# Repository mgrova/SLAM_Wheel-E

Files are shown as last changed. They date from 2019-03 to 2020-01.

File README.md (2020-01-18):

# SLAM_Wheel-E
Este es un proyecto en el cual se busca realizar una comparativa de diferentes técnicas de SLAM empleando un robot movil diferencial tipo Rover.

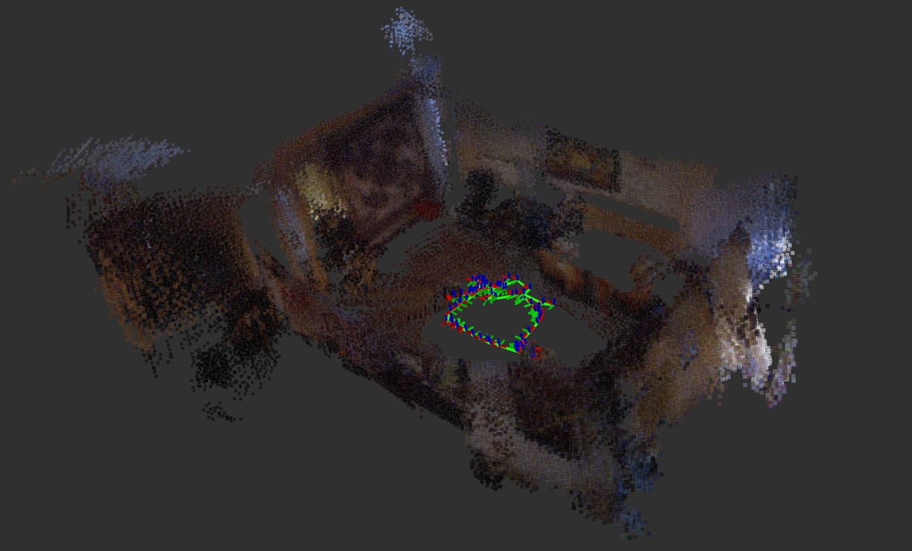
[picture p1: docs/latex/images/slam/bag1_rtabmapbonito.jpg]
RTABmap


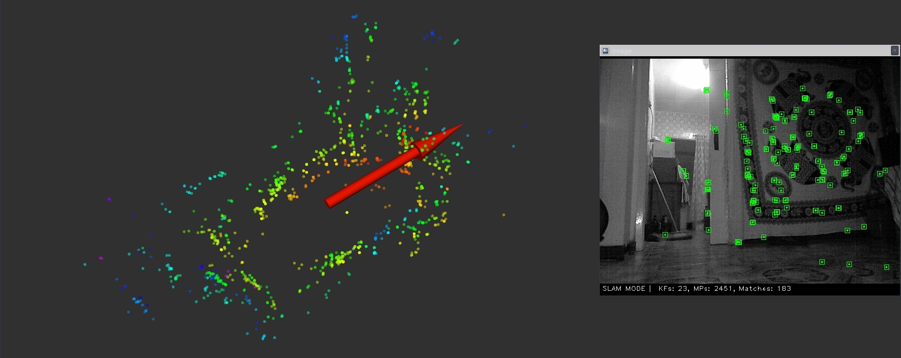
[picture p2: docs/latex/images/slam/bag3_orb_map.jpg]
ORB


# Wheel-E 
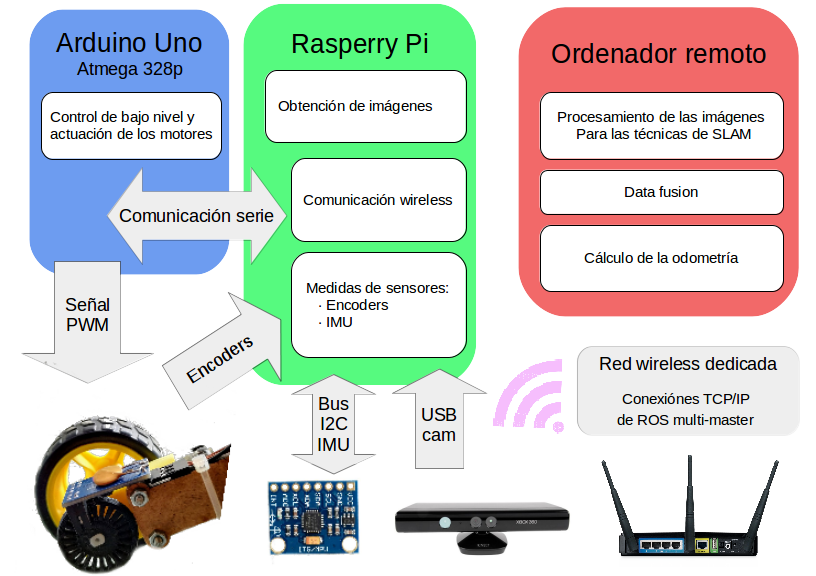
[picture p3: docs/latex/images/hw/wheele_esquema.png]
wheele_esquema


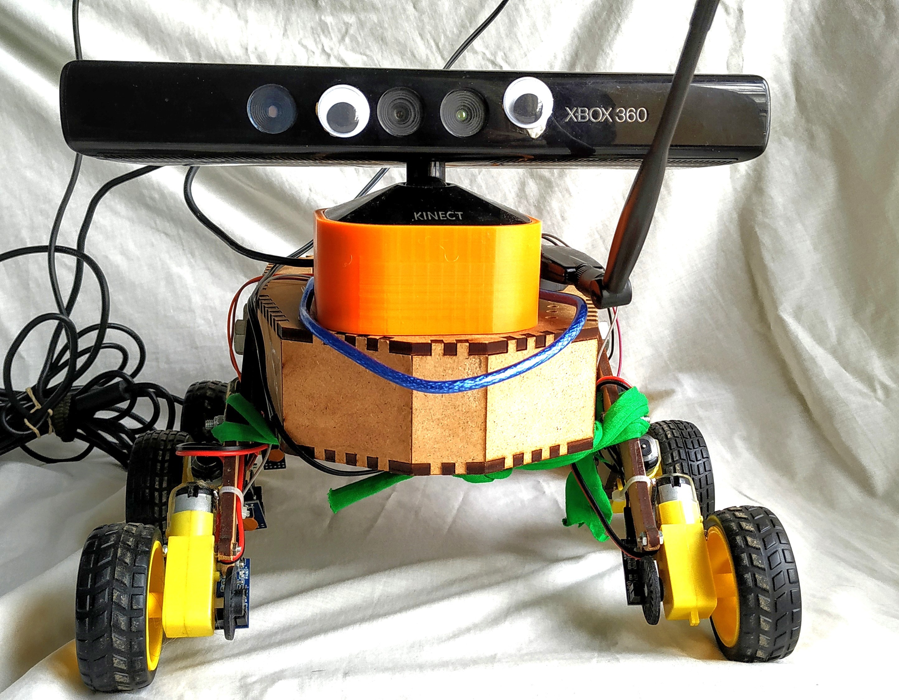
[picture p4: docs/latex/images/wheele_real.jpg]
wheele


Un análisis en detalle de todo el proyecto, así como de sus resultados se encuentra (en español) [aquí](doc.md). Los recursos bibliográficos disponibles se pueden consultar en [docs/](SLAM_Wheel-E/docs/). 

# DEPENDENCIAS
## Uso de lod gpio de la RPi
Se hace uso de la libreria pigpio:(http://abyz.me.uk/rpi/pigpio/download.html)

```
wget abyz.me.uk/rpi/pigpio/pigpio.tar
tar xf pigpio.tar
cd PIGPIO
make
sudo make install
```

## Comunicación Serial RPi-Arduino
Se hará uso de la librería de Python:

https://github.com/harmsm/PyCmdMessenger

Destacar que se emplará python2.7 y no python3.

## Comunicación multimaster(https://wiki.ros.org/multimaster_fkie)
Para comunicar la RPi y el PC, es necesario tener instalado el siguiente paquete:

```
sudo apt install ros-kinetic-multimaster-fkie
sudo apt install ros-kinetic-multimaster-launch
```

## Drivers Kinect v1 (RGB-D Camera)
Se emplearán tanto los driver necesarios para leer la IMU de la cámara y mover su motor cómo los que permiten que se pueda correr la cámara.

 - Drivers Cámara principales
```
sudo apt install ros-kinetic-freenect-stack<
```

 - Driver IMU y motor de la cámara(https://wiki.ros.org/kinect_aux)
```
sudo apt-get install libusb-1.0-0 libusb-1.0-0-dev
```
```
cd ~/catkin_ws/src
git clone https://github.com/muhrix/kinect_aux.git -b indigo
cd ~/catkin_ws
catkin_make
```

## RTAB-Map SLAM
Se deberan tener instalados los siguientes paquetes de ros y sus respectivas dependencias:
```
sudo apt-get install ros-kinetic-rtabmap-ros
sudo apt-get install ros-kinetic-octomap-*

```

## ORB-SLAM2
Se enlaza directamente al repositorio original.
https://github.com/appliedAI-Initiative/orb_slam_2_ros

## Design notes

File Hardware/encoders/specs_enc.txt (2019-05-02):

Using the following options:

hub_diameter = 10.5
set_screw_nut_thickness = 2
set_screw = 0
set_screw_nut_diameter = 5
set_screw_diameter = 3
slit_ratio = 0.5
shaft_type = 2
shaft_flat_depth = 0.8
hub_height = 4
outer_diameter = 30
slit_length = 6
shaft_diameter = 5.3
shaft_goes_through_encoder = 1
rim_width = 1.75
wheel_height = 2.6
set_screw_nut = 1
slit_count = 24

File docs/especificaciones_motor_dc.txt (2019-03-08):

especificaciones motor dc

 1. tensión : CC 3V - 6v
 2. corriente : 100 mA- 120mA
 3. tasa de reducción : 48 : 1
 4. rpm (con neumáticos ) : 100-240
 5. diámetro de los neumáticos : 65mm
 6. la velocidad del vehículo (m / minuto ) : 20-48
 7. peso del motor ( g): 29 / cada una
 8. tamaño del motor : 70mm x 22mm x 18mm
 9. Ruido: \u003c65db

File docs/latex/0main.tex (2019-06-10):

\documentclass[a4paper,twoside]{article}

%% Language and font encodings
\usepackage[spanish]{babel}
\usepackage[utf8]{inputenc}
\usepackage[T1]{fontenc}

%% Sets page size and margins
\usepackage[a4paper,top=3cm,bottom=2cm,left=2.5cm,right=2.5cm,marginparwidth=0.5cm]{geometry}

\usepackage{amsmath}			%Paquete matemático
\usepackage{graphicx}
\usepackage[colorinlistoftodos]{todonotes}

\usepackage{hyperref}		%Paquete empleado para colocar hipervinculos
\hypersetup{
 colorlinks = true,
 linkcolor = black,
 urlcolor = red
}

\usepackage{eurosym}
\usepackage{pdfpages}			%Sirve para incluir PDF en el documento
\usepackage{anysize}			%Podremos colocar imagenes de cualquier tamaño
\usepackage{subfig}				%Nos permitira colocar varias imagenes en una figura
\usepackage{float}				%Podremos crear y colocar boxes donee queramos
\usepackage[export]{adjustbox}

%Colocamos cabeceras y pies de pagina
%(CONSULTA: http://edicionesoniricas.com/maquetar-latex-encabezados-pies-pagina/)
%(CONSULTA2: https://es.sharelatex.com/learn/Headers_and_footers)
%\bfseries es análogo a \textbf{}
% \leftmark-> Adds name and number of the current top-level structure (section for article) in uppercase letters.
%\rightmark-> Adds name and number of the current next to top-level structure (subsection for article) in uppercase letters.
\usepackage{fancyhdr}		%Paquetes necesarios
\pagestyle{fancy}			%Borra los parametros por defecto
\fancyhf{}
\fancyhead[RO,LE]{\bfseries\thepage}
\fancyhead[LO,RE]{\bfseries\rightmark}
%Nos aseguramos de que en las paginas plain, no haya ni cabeceras ni lineas
\fancypagestyle{plain}
{
 \fancyhead{} % elimina cabeceras en paginas "plain"
 \renewcommand{\headrulewidth}{0pt} % así como la raya
}

%Definimos las lineas divisoras de las cabeceras y pie de pagina
\renewcommand{\headrulewidth}{1pt}	%Define el grosor de la línea de head
\renewcommand{\footrulewidth}{0pt}		%Define el grosor de la linea foot (Si no queremos linea, 0pt)
\addtolength{\headheight}{0.5pt} % espacio para la raya

%Librerias para introducir código de Matlab
%\usepackage{bigfoot} % to allow verbatim in footnote
\usepackage[numbered,framed]{matlab-prettifier}
\lstset{
 style              = Matlab-editor,
 basicstyle         = \mlttfamily,
 escapechar         = ",
 mlshowsectionrules = true
}
\usepackage{listings}
\usepackage{xcolor} % for setting colors

% Pie de pagina
%\fancyfoot{} % limpia el pie
\fancyfoot[C]{- \thepage -} % número de página centrado

%Nos generará texto para pruebas de maquetado
\usepackage{lipsum}

% To include code in differents languages
%\usepackage{minted}
%\usemintedstyle{borland}
%\usepackage{mdframed}

% To can use multirow
\usepackage{multirow}
\usepackage{comment}
\usepackage{cite}
%----------------------------------------------------------------------------------------------------------------------------------
\begin{document}
\bibliographystyle{ieeetr}
\begin{titlepage}
\centering
\Huge{\textbf{AMPLIACIÓN DE ROBÓTICA}} \\
\Huge{Comparativa de técnicas de SLAM empleando un robot movil}\\
\vspace{0.5cm}
\LARGE{Grado en Ingeniería Electrónica, Mecatrónica y Robótica}\\
\rule{\textwidth}{0.1mm}
\begin{figure}[h!]
	\centering
	
	
\end{figure}
\vspace{0.1cm}
\rule{\textwidth}{0.1mm}
\Large{\textbf{Autores:} \\
                         López Gil, Miguel \\
                         Montes Grova, Marco Antonio\\
                         Osuna Cañas, Alfonso Carlos}
\end{titlepage}
\newpage
\tableofcontents
\newpage
% %%%%%%%%%%%   INTRODUCCION %%%%%%%%%%%%%%%%%%
\section{Introducción al proyecto}
En este proyecto se implementan diferentes técnicas de SLAM visuales, así como diversas fuentes de odometría, sobre un robot móvil de bajo presupuesto. El objetivo final ha
sido diseñar e implementar una plataforma de desarollo donde poder estudiar los conceptos vistos durante el curso. Para ello, y teniendo en mente el tiempo y los recursos 
limitados de los que se disponen, se han optado por soluciones baratas o fabricadas \textit{in-house} y de sencilla implementación para favorecer un rápido prototipado.
\begin{figure}[h!]
	\centering
	
	\caption{El robot, también conocido como \textit{Wheel-E}}
\end{figure}

El robot, o, como ha sido apodado cariñosamente; \textit{Wheel-E}, consta de una \textit{Raspberry Pi 3B+} como ordenador de a bordo, que hace de interfaz con la cámara, lee 
las medidas de los encoders y establece un bus i2c con una IMU \textit{mpu-6050}. Un microcontrolador ATmega328 de una placa Arduino, comunicado por puerto serie con la
Raspberry, ejecuta un PI y actúa sobre los motores.\\

Como drivers para los motores se han usado tres circuitos integrados \textit{L293D} (dos puentes H por cada chip), que reciben como \textit{input}
una señal generada por el micro mediante \textit{Pulse-Width Modulation}. En la sección de hardware de este mismo documento se detallan en más profundidad los sistemas
electrónicos empleados, los buses de comunicaciones y se discute la estructura del robot.\\
La odometría del robot se obtiene a partir de una estimación de la posición a partir de encoders ópticos y de la velocidad y aceleración medidas por la IMU. La fusión
sensorial se realiza con un filtro de Kalman extendido, implementado en el paquete \textit{robot localization} de ROS. El código desarollado para este proyecto y el uso de 
software externo es expuesto en la sección tres de este mismo documento.\\ 
El código se puede encontrar de forma íntegra en el repositorio \url{https://github.com/marrcogrova/SLAM_Wheel-E} con licencia libre.\\

Todo el sistema, exceptuándo el control de bajo nivel del micro, corre en ROS Kinetic, en una configuración de multi-masters que relega los procesos computacionalmente costosos
(algoritmos de SLAM y fusión sensorial) a un portátil conectado a la Raspberry a través de una red \textit{Wireless} dedicada.\\

Para obtener información visual del entorno, se emplea un sensor RGB-D, la cámara \textit{Kinect v1 for Xbox 360} de Microsoft.
Más adelante, se expone en profundidad una breve explicación teórica de las metodologías SLAM y una comparativa de dos técnicas: \textit{RTAB-Map} y \textit{ORB-SLAM 2}. Adicionalmente, se prueba un software de optimización de mapas denominado \textit{Octomap}, el cual ayudará a obtener el mapa de ocupación 2D y 3D.

\newpage
\input{1hard.tex}

\newpage
\input{2soft.tex}

\newpage
\input{3slam.tex}

\newpage
\section{Conclusiones del proyecto}
En este proyecto, el objetivo principal ha sido abordar el problema completo del SLAM. Desde el diseño de un robot de bajo coste, empleando hardware barato, lo cual ha supuesto
un añadido de complejidad, hasta la implementación una técnica de SLAM. Sin embargo, gracias a los filtros estadísticos implementados, ha sido posible solventar el problema que conllevaría las deficientes medidas 
del entorno tomadas por el robot construido. \\
Para poder llegar a obtener dichas medidas ha sido necesario diseñar toda una arquitectura software tanto para realizar un control  a bajo como a alto nivel del robot. \\
Gracias a ello, ha sido posible implementar metodologías de SLAM realimentando con éstas medidas estimadas por el filtro llegando a los resultados satisfactorios mostrados anteriormente.

\bibliography{cites}
\nocite{murORB2}
\nocite{rtabmap}
\nocite{hornung13auro}
\nocite{MooreStouchKeneralizedEkf2014}
\nocite{PyCmdMessenger}
\nocite{CmdMessenger}
\nocite{WinNT}
\nocite{atmega}
\nocite{mpu6050_datasheet}
\nocite{mpu6050_regmap}
\nocite{intSLAM_I}
\nocite{intSLAM_II}
% \url{http://introlab.github.io/rtabmap/} \\
% \url{https://introlab.3it.usherbrooke.ca/mediawiki-introlab/images/7/7a/Labbe18JFR_preprint.pdf} \\
% \url{https://introlab.3it.usherbrooke.ca/mediawiki-introlab/images/b/bc/TRO2013.pdf}
\end{document}

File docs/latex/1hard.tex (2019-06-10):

\section{Hardware empleado en el proyecto}
Con el fin de obtener una vista general de todo el proyecto, así como del coste del mismo se lista a continuación todos los componentes del robot y su coste:
\begin{itemize}
	\item \textbf{Chasis del vehículo}. Fabricado a partir de un tablón plano de edf cortado en una CNC láser de forma gratuita gracias al Fablab de la Universidad de Sevilla en la facultad de Arquitectura.
	\item \textbf{Motores de corriente continua}($\approx$ 10 euros). Adquiridos a través de tiendas digitales destinadas a la importación por un precio muy ajustado, tal y como se refleja en la calidad del producto. Sin embargo, formaban parte de un kit que incluye ruedas y acople al eje de transmisión, suponiendo un ahorro importante de tiempo y dinero. 
	\item \textbf{Encoders ópticos} (6 euros). Compuestos por un diodo emisor de luz (comprados también en los mismos sitios web que los motores) y por un disco que interrumpe el paso del haz lumínico diseñado específicamente e impreso en 3D.
	\item \textbf{Microcontrolador ATmega328} ($\approx$ 10 euros). Aunque la gran parte del código implementado en el micro no utiliza las librerías de arduino, por comodidad se ha optado por un microchip ya montado en una placa tipo arduino (un modelo no oficial, clónico).
	\item \textbf{IMU MPU-6050} (3 euros). Con la capacidad de medir velocidades y aceleraciónes el los tres ejes del espacio.
	\item \textbf{Raspberry Pi 3B+} (30 euros). Constituye el cerebro del robot, y centraliza la comunicación con los demás sistemas. Aunque puede resultar el componente más caro del proyecto, se disponían de varias de antemano, por lo que no hubo que asumir su coste.
	\item \textbf{Kinect for Xbox 360 V1} (15 euros). Esta popular cámara merece la fama que tiene por lo asequible que es (especialmente el modelo más antiguo) y las utilidades que trae. Se demuestra como la opción más socorrida para desarollar con poco presupuesto aplicaciones que requieran de imágenes o sensores de profundidad.
\end{itemize}
\subsection{Chasis del vehículo}
El robot ha sido diseñado con una topología inspirada en los vehículos de exploración espacial conocidos como \textit{ROVERS}, utilizando materiales y métodos de construcción asequibles y
manteniendo como objetivo una posible sencilla sustitución de cada componente. \\
Algunos elementos sin funcionalidad estructural, como los encoders o el soporte de la cámara, han sido fabricados mediante impresión 3D. \\
Todos los modelados pueden encontrarse en la sección hardware del repositorio de \textit{Git-Hub}.
\begin{figure}[h!]
	\centering
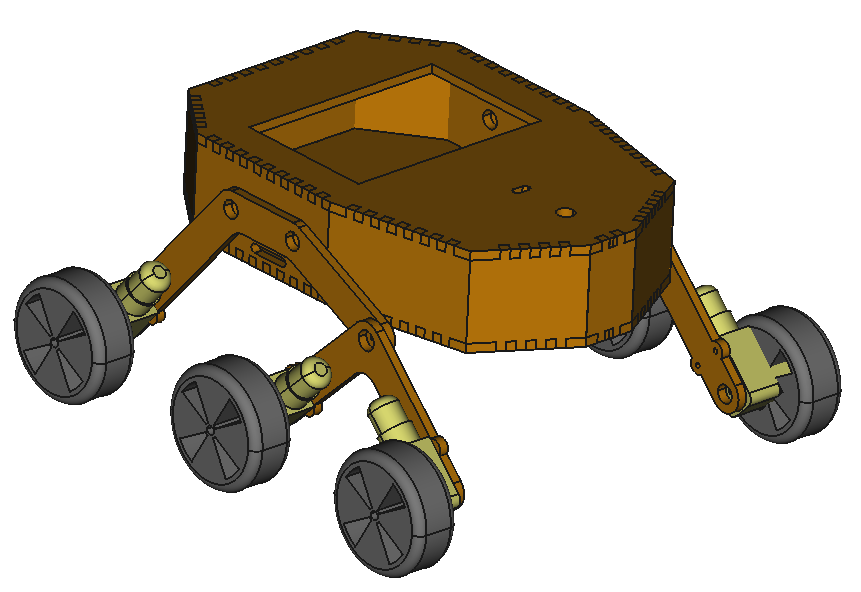
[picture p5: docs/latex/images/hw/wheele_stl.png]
	
	\caption{Modelo CAD del robot}
\end{figure}
\\
La disposición geométrica es la de un vehículo diferencial, con tres pares de ruedas, cada una con su respectiva pareja de motor y encoder.\\

\subsection{Motores DC}
 Los seis motores utilizados, a pesar de que deberían comportarse de forma parecida, presentan respuestas muy diferenciadas; para una señal de control idéntica cada uno de ellos muestran puntos de operación distintos y se observan respuestas ante escalón muy variadas. Sin embargo, 
 todos presentan un comportamiento común, una gran zona muerta que complicará mucho la operación del robot a velocidades extremadamente bajas. En concreto, con el convesor digital-analógico del microcontrolador seleccionado, se pierden un 40\% de los bits del rango de salida a causa de este incoveniente.  
\subsubsection{Especificaciones}
\begin{itemize}
	\item Tensión de trabajo: 3-6 V.
	\item Corriente máxima: 120 mA.
	\item Dimesiones: 70x22x18 mm.
	\item Reductora: 48 revoluciones a una.
	\item Peso (sin ruedas): 29 gramos.
\end{itemize}

A continuación, se muestra la caracteristica estática obtenida para uno de los motores, la caracterización para el resto de ellos se ha realizado de forma análoga. 
\begin{figure}[h!]
	\centering
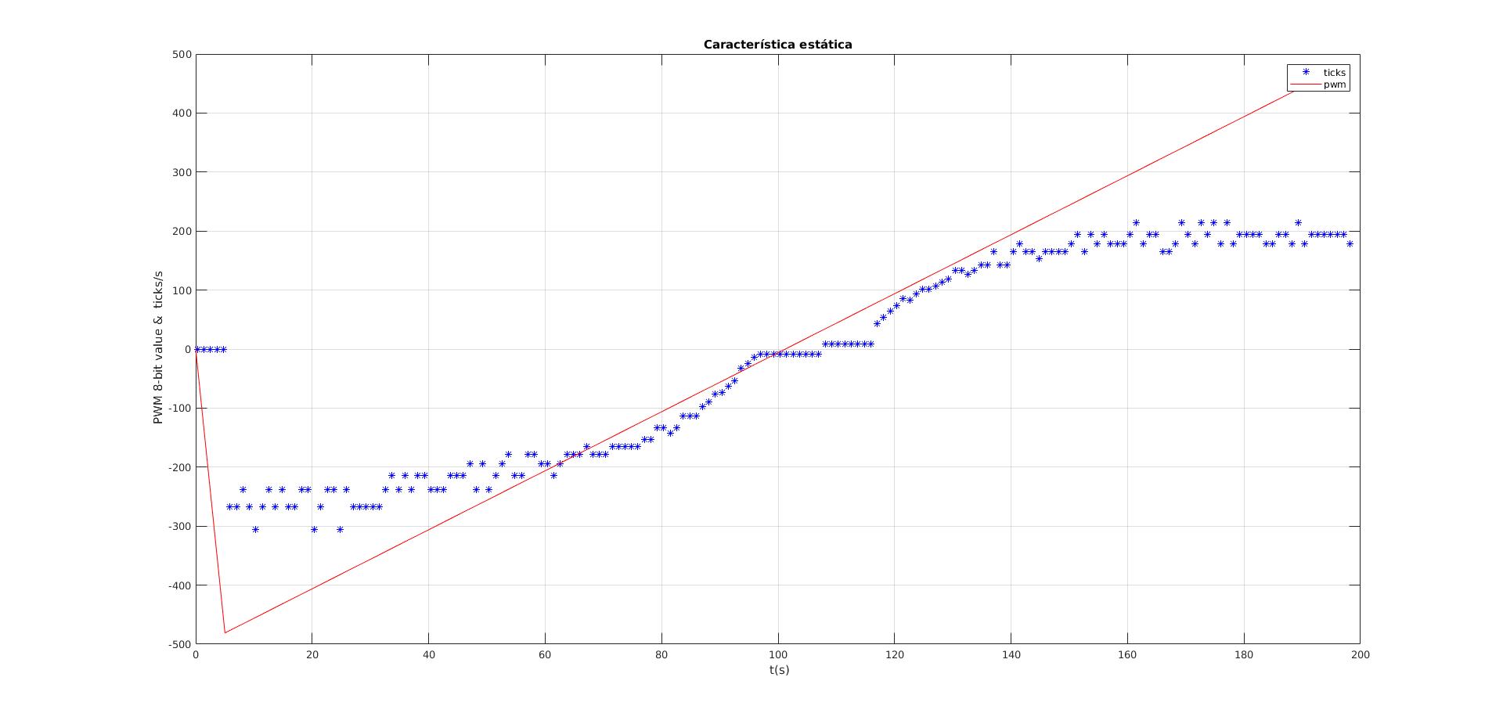
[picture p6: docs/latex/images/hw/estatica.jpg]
	
	\caption{Característica estática de un motor}
\end{figure}

\subsubsection{Drivers}
Se han empleado tres microchips L293D que integran cada uno dos puentes H. Estos puentes H nos permiten configurar la dirección de giro con dos señales digitales y la velocidad con otra señal analógicas.\par
Por comodidad y robustez, se ha diseñado en \textit{KiCad} una placa de circuito impreso muy simple que facilita el cableado y permite integrar algún 
componente pasivo (como diodos fly-back o capacidades de by-pass).
Gracias al laboratorio de electrónica, este diseño ha sido revelado sobre una placa de una sola cara, obteniendo, como se aprecia en las imágenes, 
un acabado final bastante bueno.
 \begin{figure}[h!]
	 \centering
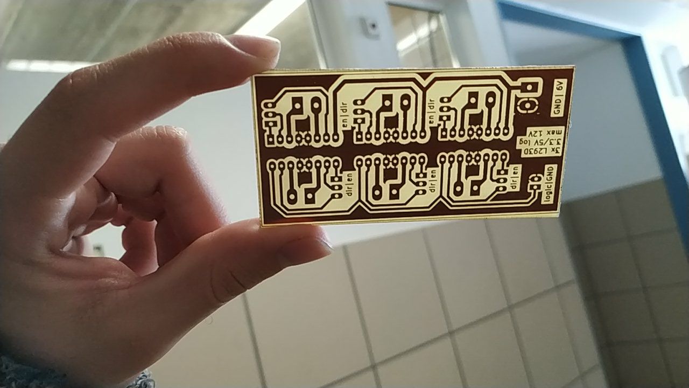
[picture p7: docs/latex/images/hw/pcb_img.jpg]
	 
 	
 	\caption{Diseño en KiCad de la PCB.}
 \end{figure}
 \par
Los integrados requieren de una referencia de tensión lógica de 5V y una alimentación para los motores de 6V.
La referencia lógica proviene, obviamente, del Arduino. Los motores sin embargo son alimentados con una fuente externa de 6V y 2A máximo. \\

\subsection{Encoders}\label{enc_hard}
Los sensores elegidos para medir la velocidad de cada rueda y estimar la posición y velocidad del robot, son unos sencillos encoders ópticos binarios junto a unos discos perforados. Al pasar la luz por una perforación del disco, 
que gira a la misma velocidad que la rueda, se manda una señal digital al micro. Contabilizando los flancos de subida o de bajada en cierto periódo de tiempo, y conociendo las dimensiones del disco, se obtiene una estimación de 
la velocidad.
 \begin{figure}[h!]
 	\centering
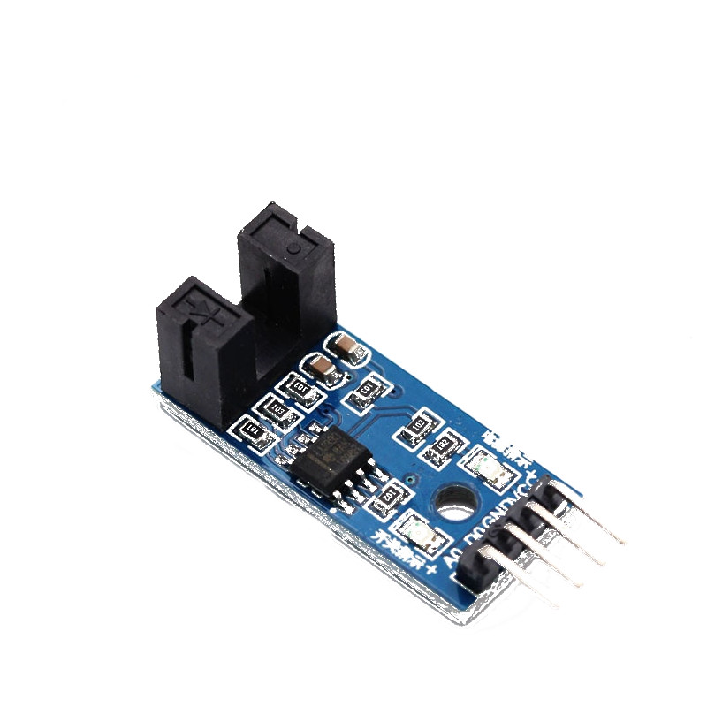
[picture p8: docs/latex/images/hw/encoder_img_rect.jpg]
	 
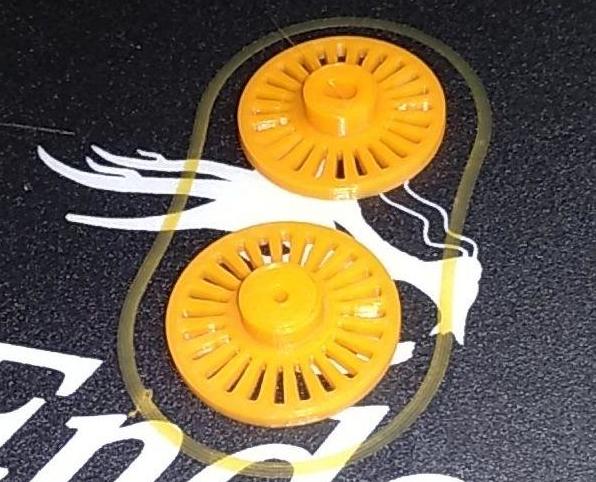
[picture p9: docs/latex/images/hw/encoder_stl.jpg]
	 
 	\caption{Encoder óptico y disco empleados}
 \end{figure}

\subsection{IMU}\label{imu_hardw}
Como ya se ha mencionado con anterioridad, se ha escogido una IMU MPU-6050 de seis grados de libertad para obtener datos de las velocidades y aceleraciones del robot. El microchip contine varios subsitemas, de los cuales interesa resaltar especialmente:
\begin{itemize}
	\item Giroscópio (tres ejes), con un rango progamable de ±250, ±500, ±1000 y ±2000 (°/s).
	\item Acelerómetro (tres ejes), con un rango progamable de ±2g, ±4g, ±8g y ±16g.
	\item Conversores analógico-digitales de 16 bits para las salidas del giroscópio y del acelerómetro.
	\item Bus i2c para ejecutar operaciones de lectura y escritura en cualquier registro del chip a una frecuencia máxima de 400kHz.
	\item Bus de comunicación auxiliar que posibilita introducir un magnetómetro en el futuro sin modificar el conexianado de todo el sistema.
\end{itemize}
Puesto que la IMU consume muy poca potencia en todo momento, se puede alimentar sin problemas desde cualquier salida de referencia de la Raspberry. \\
\begin{comment}
A continuación, se mostrará una imagen de la IMU conectada: YO ESTO LO QUITARIA PORQUE CON EL PIE DE FOTO ES ENOUGH
\end{comment}
\begin{figure}[h!]
	\centering
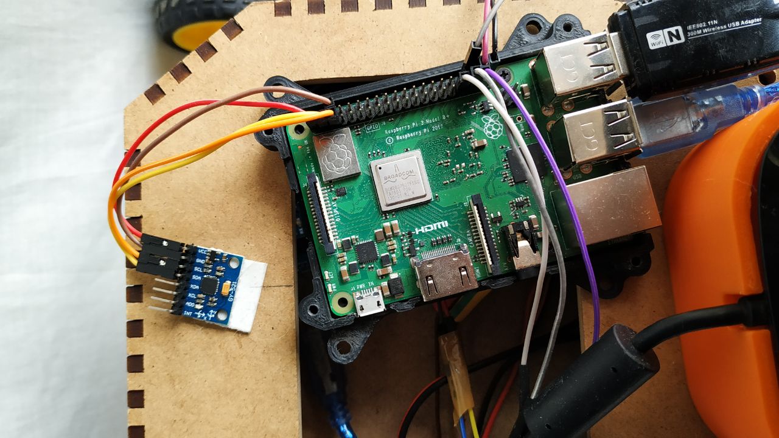
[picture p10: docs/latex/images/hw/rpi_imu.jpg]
	
	\caption{Conexionado entre la RPi y la IMU por $I^2C$}
\end{figure}

\subsection{Raspberry Pi}
Este \textit{single-board computer}, como se le denomina en inglés, alberga muchas posibilidades. En el centro de todas ellas se encuentra un procesado ARM Cortex-A53 de 64-bit a 1.4Ghz capaz de correr varias distribuciones de GNU/Linux. \\
Con la limitada potencia gráfica de la que dispone, y su único gigabyte de memoria RAM; resulta necesario procesar los cálculos más complejos en otro sistema más potente.\\
El modelo utilizado (3B+) incluye WiFi 802.11n a 150Mbit/s máximo. Sin embargo, es conveniente usar una antena WiFi externa más potente para conseguir más rango de señal.\\
La Raspberry es alimentada a través de un puerto micro USB a 5V con una corriente máxima de 2.5A, aunque su lógica funciona a 3.3V.

\subsection{Arduino Uno}
Por conveniencia se ha optado por una placa arduino, que además de un microcontrolador ATmega328p, integra un puerto usb con un chipset que facilita su programación y la comunicación serie con el mismo. Incluye también un cristal de cuarzo , que provee una fuente prescisa para la señal de reloj y resulta especialmente útil para implementar el control de bajo nivel en tiempo real.
El micro cuenta con una memoria flash progamable de 32 kilobytes y una eeprom de un kilobyte, que es más que suficiente para el uso que se le va a dar. Dos timers de 8 bits y otro de 16 bits generan las interrumpciones necesarias para controlar el tiempo real e implementar el control. De todas las 23 posibles entradas/salidas digitales del micro, se ocupan cuatro salidas para seleccionar el sentido de la marcha de los motores (dos para todos las ruedas de la izquierda y dos para las de la derecha) y seis canales PWM para controlar la velocidad individual de cada uno.\\
\newpage
\begin{figure}[h!]
	\centering
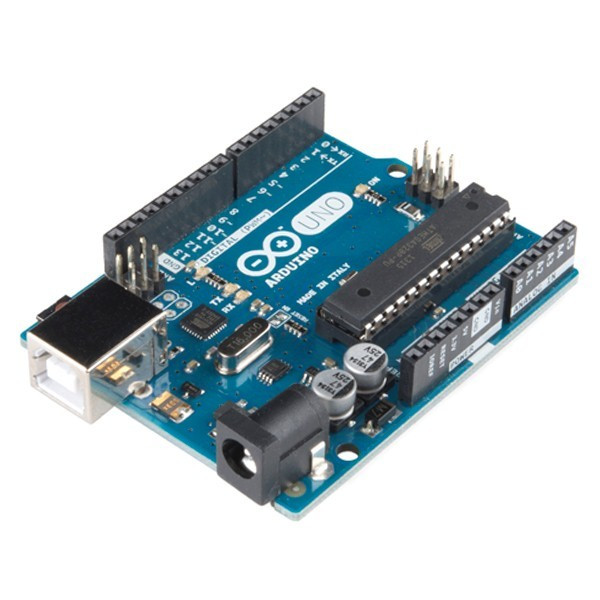
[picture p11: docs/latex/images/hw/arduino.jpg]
	
	\caption{Microcontrolador empleado para la comunicación a bajo nivel}
\end{figure}
\par
La potencia eléctrica necesaria para que el micro, y sus periféricos, operen correctamente (5V y menos de 100mA) se obtienen por el puerto USB desde la Raspberry Pi, aprovechando el bus de comunicación serie.

\subsection{Cámara}
La \textit{Kinect for Xbox 360 V1} integra una cámara RGB y un sensor de profundidad de luz infrarroja estructurada. El rango del sensor de profundidad esta comprendido entre los 0.7 y los 6 metros. El campo de visión del
dispositivo es de 57º horizontalmente y 43º en la vertical, aunque cuenta con un soporte motorizado que controla el \textit{pitch} de la camara con un rango de ±27º. La resolución máxima de la cámara es de 1280x1024 píxeles,
siendo la más usada 640x480 píxeles; puesto que el \textit{frame rate} depende fuertemente de la resolución con la que se trabaje. \\
El calculo de la profundidad se realiza a partir de la matriz proyectada.
\begin{figure}[h!]
	\centering
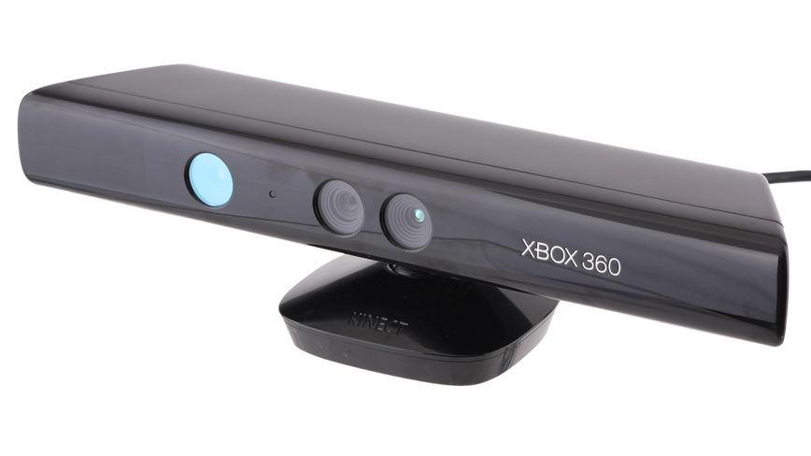
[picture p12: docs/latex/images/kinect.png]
	
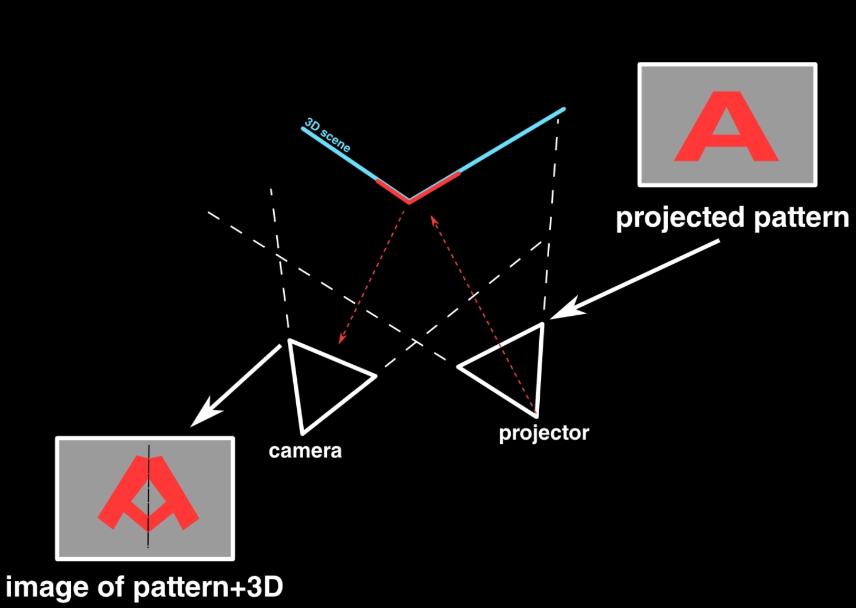
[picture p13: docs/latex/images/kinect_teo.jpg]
	
	\caption{Cámara RGB-D Kinect y esquema del cálculo de profundidad}
\end{figure}

\newpage
\subsection{Esquema de comunicación del hardware}
Debido a la multitud de entradas y salidas digitales y analógicas necesarias, al coste computacional de todo el sistema, y a la variedad de las comunicaciones, se plantea una configuración muy modular 
entre el ordenador de abordo (la \textit{Raspberry Pi}), los periféricos y la unidad de procesamiento para las partes más pesadas del software.\\
  \begin{figure}[h!]
  	\centering
  	
  	\caption{Esquema de conexionado de todos los componentes}
  \end{figure}

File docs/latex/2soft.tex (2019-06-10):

\section{Software empleado en el proyecto}
\subsection{ROS}
ROS (Robotic Operating System) consite en un framework para la robótica sobre el que desarrolladores de cualquier 
ambito pueden aportar soluciones modulares a los sistemas de forma general. La modularidad de ROS hace que desarrollar 
un nuevo sistema o prototipo pueda ser una tarea tan sencilla como interconectar módulos de otros desarrolladores con 
los propios.
\begin{comment}
Esta característica lo hace idoneo para un proyecto como este en el que el uso de técnicas de percepción, 
mapeado, localization, etc, complejas se escapa del alcance; y solo sea necesario el desarrollo de modulos específicos de este robot
que sean capaces de comunicarse con aquellos más complejos y sean capaces de proporcionarle los datos necesarios para implementar los
algoritmos de SLAM. \\    
\end{comment}

El sistema operativo empleado tanto en el ordenador de abordo del robot,la Raspberry Pi, cómo en en el ordenador principal es Ubuntu 16.04, de tal modo que la distro de ROS en la que ha sido 
implementado el proyecto es ROS Kinetic Kame\footnote{https://wiki.ros.org/kinetic}.
\begin{figure}[!ht]
    \centering
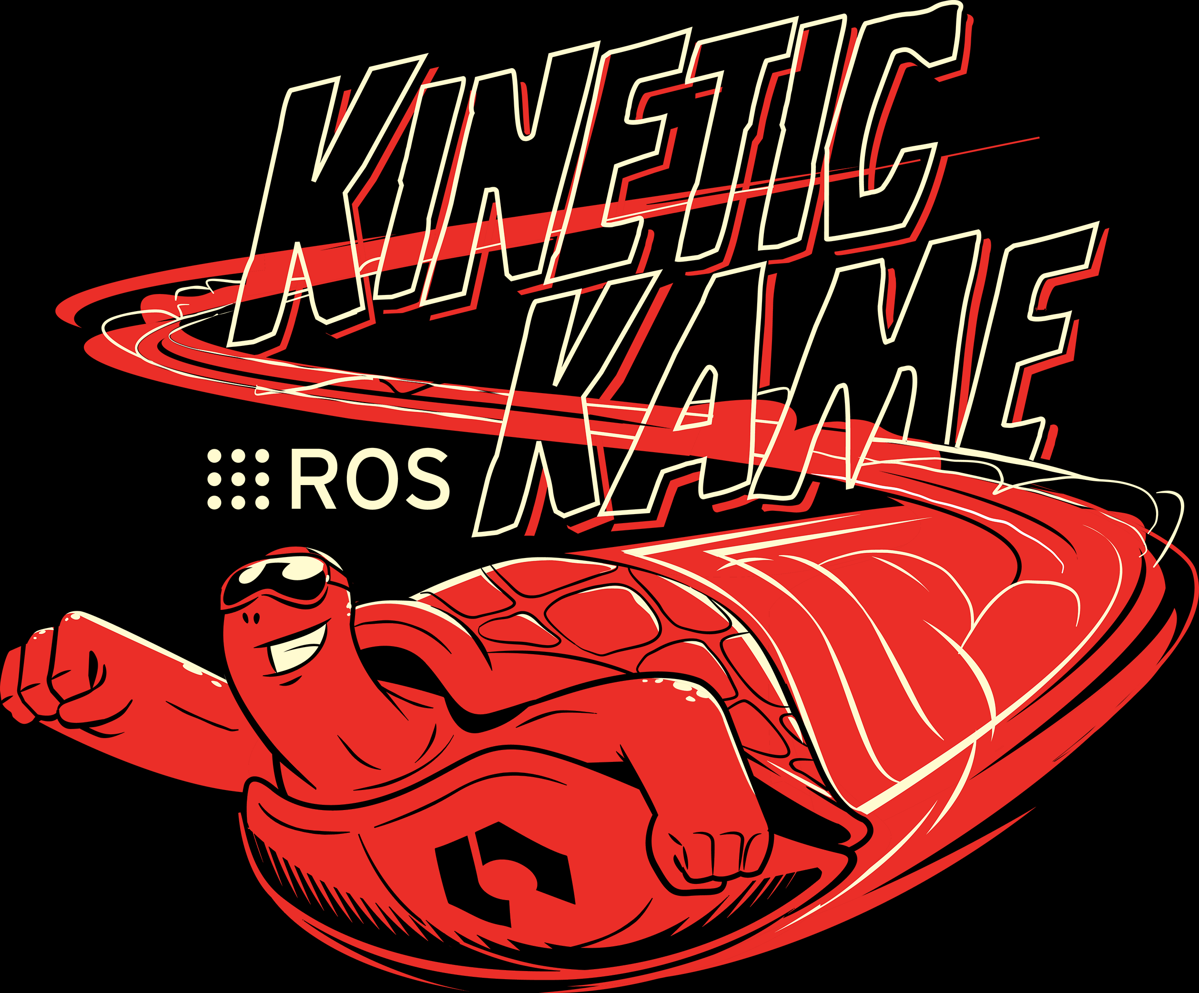
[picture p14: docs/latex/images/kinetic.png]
    
    \caption{Version de ROS empleada}
\end{figure}

\subsubsection{Interfaz con IMU}
Como ya se ha visto en la seccion \ref{imu_hardw}, al robot se le ha dotado con una IMU de seis grados de libertad con el fin de obtener medidas de aceleraciones.\\
La conexión se hace a través de una linea por protocolo $I^2C$, por lo que ha sido necesario el desarrollo de dos `wrapers' en Python con funciones de bajo nivel; uno para el acceso a las
funciones de comunicación $I^2C$ a nivel de registros hardware y otro a nivel de funcionalidades elementales para el manejo de los datos de la IMU.
Sobre ambos `wrapers' se ha escrito el nodo de ROS encargado de publicar los datos en dos `topics', \textit{imu1\_rawImu} y \textit{imu1\_scaImu}, con los datos tal y como llegan 
de la IMU en el primero y reescalados en el segundo. El tipo de mensaje en el que se publican los datos es \textit{\href{http://docs.ros.org/kinetic/api/sensor_msgs/html/msg/Imu.html}{sensor\_msgs/Imu}}.\par
Al tratarse de un sensor de bajo nivel que aporta información a los estratos más bajos del control, para poder disponer depués de mayor ancho de banda, se ha elegido una frecuencia de muestreo del sensor de $50\ [Hz]$; sufucientemente alta para no comprometer la estabildiad del sistema
pero tambien lo sufucientemente baja como para no saturar el ordenador de abordo (teniendo en cuenta que este también deberá mantener un flujo constante de imagenes capturadas por la cámara, con el coste que eso conlleva).

 \subsubsection{Interfaz con encoders}\label{enc_soft}
Otro sensor añadido son los encoders mencionados en la sección \ref{enc_hard}. Para su programación se ha desarrollado un `wraper' en C++ de la librería para Raspberr-Pi 3B \textit{pigpio} 
\cite{pigpio}. Como los encoders solo pueden ofrecer información de la magnitud de la velocidad y no del sentido de giro, es necesario realizar dicha consideración a nivel de software para poder representar esa información.
Esto se consigue suscribiéndose al `topic' \textit{cmd\_vel}, obtiniéndose así la referencia del sentido de giro a cada lado del robot. Este dato se usa para reajustar el signo de las velocidades leídas de los seis encoders y publicarlas en el topic \textit{encoders} con el tipo de mensaje \textit{\href{http://docs.ros.org/jade/api/std_msgs/html/msg/Float64MultiArray.html}{std\_msgs/Float64MultiArray}}. La medida de los encoders, al tratarse de medidas de baja calidad con valores dispersos, son filtradas y promediadas entre sí. En cuanto a la frecuencia de muestreo, se ha seguido la misma filosofia que con la programación del nodo de la IMU y se ha decido muestrear a $50\ [Hz]$.

\subsubsection{Odometría}
A partir del calculo de la velocidad obtenida desde los encoders se desarrolló un nodo en ROS en el que se calcula la odometría del robot.\\
Para ello se han hecho una serie de suposiciones y simplificaciones del modelo del robot que después, en base a los resultados obtenidos, se han demostrado bastante acertadas.
\begin{itemize}
    \item Las ruedas tienen un modelo de rodadura perfecto y no deslizan en el suelo; esto no es cierto en la práctica, y supone una fuente de errores importantes por la deriva que acumulan las posiciones estimadas. Dichos errores que son corregidos mediante una fusión sensorial.
    \item El modelo del robot consiste en un modelo diferencial de dos ruedas. En base a esto, a cada rueda `virtual' se le asigna el promedio de la velocidad de las 3 ruedas de cada bancada.
\end{itemize}
Las ecuaciones que definen el modelo del robot son las mostradas a continuación:
\begin{figure}[!ht]
    \centering
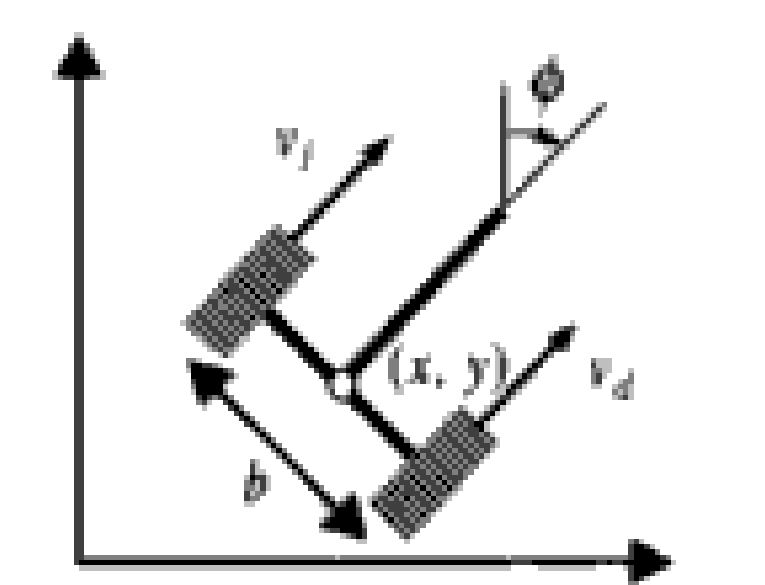
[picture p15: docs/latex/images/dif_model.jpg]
    
    \caption{Representación posición y orientación modelo diferencial}
\end{figure}
\begin{center}
    $v=\dfrac{v_{dcha}+v_{izqd}}{2}$ \hspace{2cm} $\theta=\dfrac{v_{dcha}-v_{izqd}}{b}$
\end{center}
dónde \textit{v} es la velocidad lineal, \textit{w} la velocidad angular y \textit{b} la distancia entre las ruedas.\\
Se define la posición y la orientación del robot cómo:
\begin{equation}
    \begin{pmatrix}
        \dot{x} \\
        \dot{y} \\
        \dot{\theta}
    \end{pmatrix}=
    \begin{pmatrix}
        cos(\phi) & 0 \\
        sin(\phi) & 0 \\
        0 & 1 \\
    \end{pmatrix}
    \begin{pmatrix}
        v \\
        \theta
    \end{pmatrix}
\end{equation}
\par
Este nodo se suscribe al desarrollado en \ref{enc_soft} en el `topic' \textit{encoders}, y cada vez que llega un mensaje nuevo con los datos de los 
encoders calcula el avance del robot en base al modelo propuesto. La publicación de los datos se hace en el `topic' \textit{odom} a un ratio de $25\ [Hz]$ con un mensaje del tipo \textit{\href{http://docs.ros.org/kinetic/api/nav_msgs/html/msg/Odometry.html}{nav\_msgs/Odometry}}.

\subsubsection{Interfaz Raspberry-Pi/Arduino}
La comunicación por puerto serie se implementa haciendo uso de la librería \textit{CmdMessenger} \cite{CmdMessenger}, que permite definir comandos (con la posibilidad de asociarles argumentos y callbacks) de forma eficiente y sencilla.
Por la parte de la Raspberry, se usan las librerías CmdMessenger (desarrollada en C) o su alternativa PyCmdMessenger (en Python) en el nodo \textit{serial\_com.py} para transmitir por el puerto serie. Los siguientes comandos son los más importantes: \\
\begin{itemize}
	\item \textbf{Cmd\_off} $\rightarrow$ Al recibir este comando el micro pasa a no hacer nada, comportándose como un apagado de emergencia.
	\item \textbf{Change\_ref} $\rightarrow$ Acompañado de un valor de referencia de la velocidad, que el micro usará para el control de los motores.
\end{itemize}
\par
De este modo es sencillo publicar un tópico de 'comandos del sistema', como apagar o funciones de debugeo, y otros tópicos para los datos que hayan de retransmitirse. Cuando llegan datos desde el arduino, se ejecuta un callback (de la librería externa, no de ROS) que publica dicha información el tópico correspondiente. Si es el caso contrario, y se busca enviar datos al arduino, el nodo se subscribirá al tópico con ese dato y en el callback asociado (ahora sí de ROS) se envía al arduino.

\subsubsection{Interfaz Arduino/Motores}
Una interrupción disparada a partir de uno de los timers del microcontrolador ejecuta el control de bajo nivel, garantizando un tiempo de actuación para el controlador con una periocidad constante. Al ser un vehículo puramente diferencial, todos los motores de un mismo lado se mueven en la misma dirección. Sin embargo, debido a la gran diferencia entre las respuestas de los motores, la señal de control de cada uno debe ser única. Por tanto, las señales necesarias para controlar los motores son; dos digitales por cada lado del vehículo para configurar la dirección del mismo, y una señal analógica generada por PWM para cada motor para modificar su velocidad. \\
Una vez realizados los cálculos, y escritas las señales para controlar los motores, se procede, si da tiempo antes de la próxima ejeccución de la interrupción, a recibir referencias u órdenes desde la Raspberry Pi. El control es un simple PI cuyas ganancias han sido ajustadas experimentalmente, con un \textit{anti-windup} con constante de tiempo configurable.

\subsubsection{Computación distribuida con ROS-Multimaster Package}
Las técnicas de SLAM a testear en el robot desarrollado son computacionalmente costosas. Todo este coste computacional es
imposible asumirlo desde una Raspberry-Pi, por lo que surge la necesidad de hacer el procesado en un servidor remoto \textit{on the fly} con las 
dificultades que eso conlleva, entre ellas y la más importante, la sincronización de datos. Bajo estas condiciones de diseño y restricciones aparece una solución de la comunidad: ROS multimaster\_fkie. La premisa que lo rige es simple, dado un sistema mutirobot cada elemento mantiene la ejecución de dos nodos locales, \textit{master\_discovery} y \textit{master\_sync}; el primero es el encargado de mantener una lista del resto de \textit{roscores} disponibles en la red y de publicar el suyo propio como activo, el otro es el encargado de suscribir su \textit{core} a los nodos de otros \textit{cores}. Así, todas las unidades de procesamiento tienen acceso a los recursos del resto. 
\begin{figure}[!ht]
    \centering
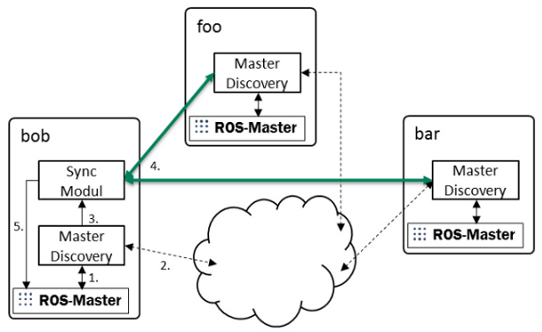
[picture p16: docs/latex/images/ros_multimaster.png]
    
    \caption{Esquema del funcionamiento básico del paquete Multimaster}
\end{figure}

En este proyecto, su integración se ha llevado a cabo lanzando en la Raspberry-Pi y en otro PC los nodos correspondientes; siendo la Raspberry-Pi la 
suministradora de información y el PC el encargado de procesarla.

\subsection{Implementación filtro estadístico}
Debido a los múltiples sensores que integra el robot, a la variedad de sus medidas y a las incertidumbres, desconocidas, a la que están sujetos, se ha considerado necesario y tremendamente benificioso la implementación de algún tipo de \textit{Data Fusion}. Con este objetivo se introduce un filtro estadístico, de Kalman, para estimar el vector de estados del vehículo. La razón por la que se ha elegido este filtro frente a otros, por ejemplo un filtro de información, se debe a la simpleza del modelo de observación, pues las posibles entradas son meramente la odometría de los encoders, las medidas de la IMU y la odemetría visual.

\subsubsection{Filtro de Kalman Extendido}
La información que el sistema obtiene de los sensores está sujeta a ruido e incertidumbres de la medida. A fin de minimizar los errores y mejorar la estimación de la posicion y velocidad del robot se ha 
considerado que era de especial interes y utilidad la aplicación de un filtro recursivo Bayesiano como estimador de estados, en concreto el filtro de Kalman extendido. \\
Este filtro es una extensión del filtro de Kalman para sistemas no lineales.
\begin{figure}
    \centering
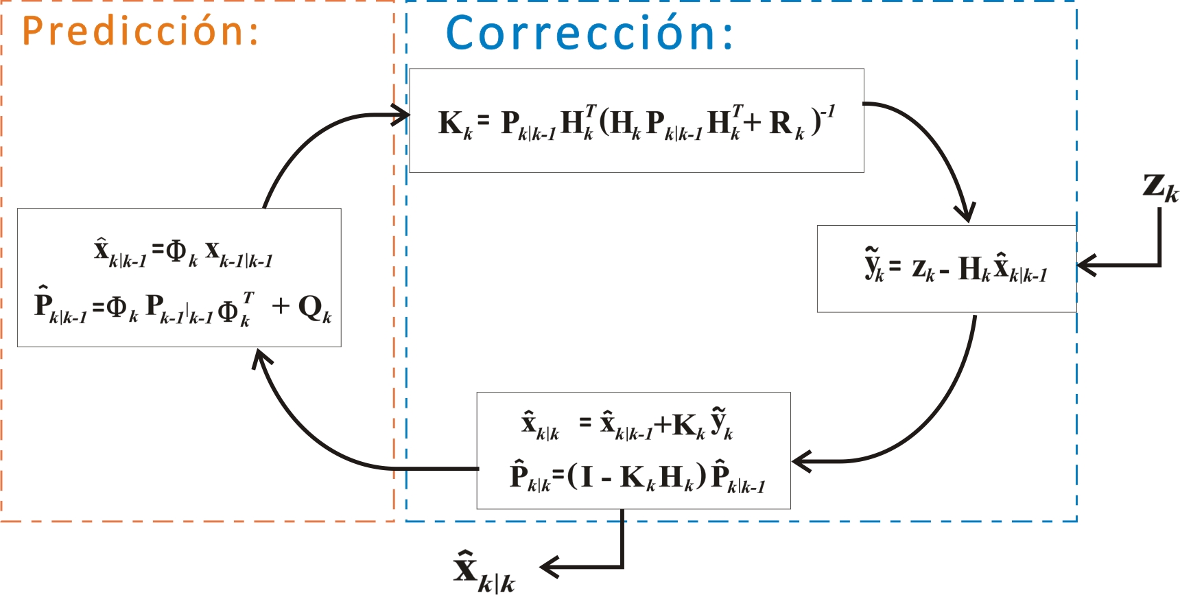
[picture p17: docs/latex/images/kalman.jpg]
    
    \caption{Representación del filtro de Kalman. Fuente: Wikipedia}
\end{figure}

\subsubsection{ROS-Robot Localization Package}
Como implementación del EKF se ha decidido usar el paquete de ROS kinetic \textit{Robot Localization}\cite{MooreStouchKeneralizedEkf2014}. Este paquete contiene dos nodos de estimación de estados, uno con un filtro extendido y el segundo con un \textit{Unscented Kallman Filter}. Además integra utilidades que facilitan el uso de un sistema GPS, cuyos detalles serán ignorados aquí por resultar irrevelantes para este proyecto.\\
Las capacidades interesantes de este paquete las podemos resumir en las siguientes:
\begin{itemize}
	\item Múltiple entrada de sensores, sin restricción en número o tipo.
	\item Configuración sencilla de las entradas, pudiendo descartar ciertas medidas o corregir determinados datos de antemano.
	\item Tanto los sensores como el comportamiento del modelo se ajusta fácilmente desde un fichero yaml.
	\item Los nodos estiman un estado 15-dimensional del robot: posición (X,Y,Z), orientación (\textit{pitch},\textit{roll},\textit{yaw}), velocidad, tanto de la posición como de la orientacion, y aceleración del robot.
	\item Soporte de los mensajes de ROS para cada tipo de sensor y sus estándares.
\end{itemize} 

\newpage

\subsection{Arquitectura general del sistema}
A continuación, se mostrará la comunicación entre nodos tanto dentro de la RPi cómo en el momento de lanzar las técnicas de SLAM. En primer lugar se mostrará la estructura en el momento en el que se grabó
el \textit{bag} y, cómo sería la estructura si se realizará SLAM :
\begin{figure}[!ht]
    \centering
    
    \caption{Captura de los nodos corriendo dentro de la Rapberry Pi 3B+}
    \label{rqt01}
\end{figure}

\newpage
Si se corriese el SLAM en tiempo real, la arquitectura de nodos de ROS sería la siguiente:

\begin{figure}[!ht]
    \centering
    
    \caption{Captura de los nodos cuando se realiza SLAM en tiempo real}
    \label{rqt02}
\end{figure}

Para los experimentos, y en concreto con RTAB-Map, la estructura nodal es la siguiente:
\begin{figure}[!ht]
    \centering
    
    \caption{Captura de los nodos ejecutandose cuando se corre SLAM sobre los bags}
    \label{rqt03}
\end{figure}

\section{Puntos destacables de la implementación del proyecto}

\subsection{Obtención de los parámetros de la cámara}
Destacar que, siempre es necesario conocer los parámetros intrínsecos de la cámara además de la matriz de rotación. Para obtener la matriz de parámetros de nuestra cámara, se ha hecho uso del paquete de ROS, \textit{\href{http://wiki.ros.org/camera_calibration}{Camera\_calibration}}.\\
Este paquete nos proporcionará la herramienta mostrada a continuación, que gracias a un tablero de ajedrez nos dará los parámetros intrínsecos de nuestra cámara:
\begin{figure}[!ht]
    \centering
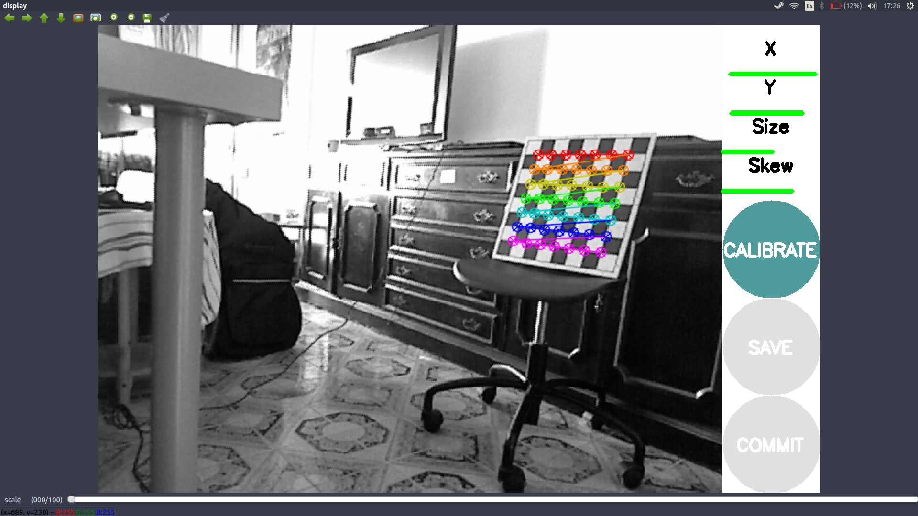
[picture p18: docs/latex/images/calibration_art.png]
    
    \caption{GUI proporcionada por el paquete ejecutándose}
\end{figure}

Las matrices serán dadas en pormato \textit{.ost} y \textit{.yaml} que, despues se le pasará cuando se quiera emplear la cámara para actualizar el topic camera\_info,cuyo 
tipo de mensaje será \textit{\href{http://docs.ros.org/melodic/api/sensor_msgs/html/msg/CameraInfo.html}{sensor\_msgs/CameraInfo}}.
\subsection{Inicialización del robot}
Para lanzar todos los nodos de ROS en el ordenador de abordo del robot y en el ordenador principal se han creado los siguientes ficheros \textit{roslaunch}:
    \begin{figure}[!ht]
        \centering
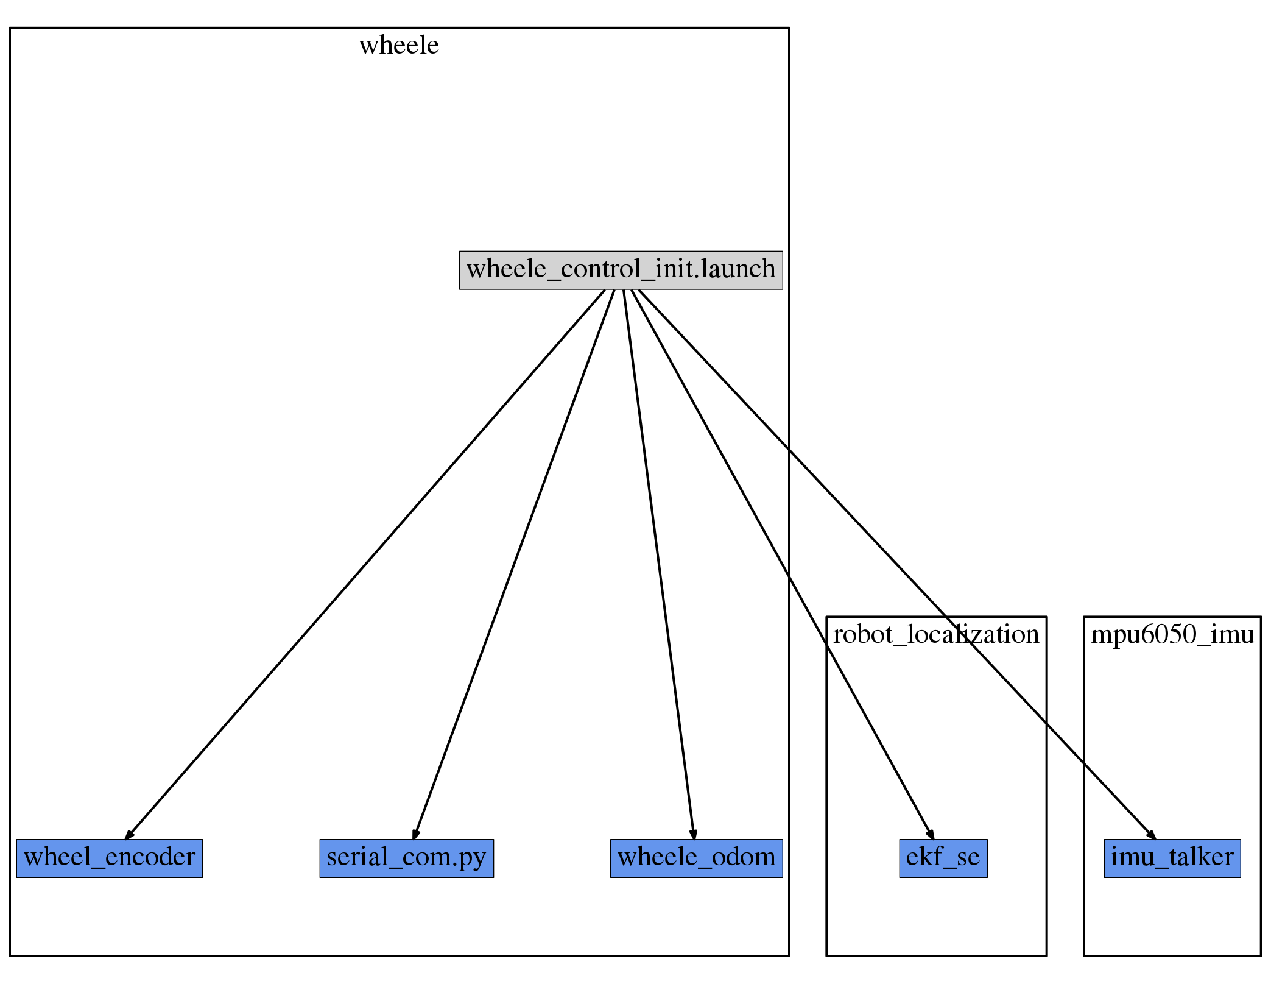
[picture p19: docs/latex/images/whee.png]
        
        \caption{Nodos lanzados en el robot}
    \end{figure}

También se lanzarán los drivers de la cámara, aunque no aparezcan en la imagen. Los drivers son proporcionados por el 
paquete de ROS \textit{\href{https://github.com/ros-drivers/freenect\_stack}{Freenect}}.
Para poder tener control del motor integrado en la cámara, se ha empleado el paquete \textit{\href{https://github.com/muhrix/kinect_aux}{Kinect-aux}}.

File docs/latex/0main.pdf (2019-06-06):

# AMPLIACIÓN DE ROBÓTICA Comparativa de técnicas de SLAM empleando un robot movil

## Grado en Ingeniería Electrónica, Mecatrónica y Robótica

## Índice

1. Introducción al proyecto | 3
2. Hardware empleado en el proyecto | 3
3. Software empleado en el proyecto | 6
4. Introducción al SLAM(Simultaneous Localization and Mapping) | 8

### 2 ÍNDICE

## Autores: López Gil, Miguel Montes Grova, Marco Antonio Osuna Cañas, Alfonso Carlos

- 2-

3

## 1. Introducción al proyecto

En este proyecto se implementan diferentes técnicas de SLAM visuales, así como diversas fuentes de odometría, sobre un robot móvil de bajo presupuesto. El objetivo final ha sido diseñar e implementar una plataforma de desarollo donde poder estudiar los conceptos vistos durante el curso. Para ello, y teniendo en mente el tiempo y los recursos limitados de los que se disponen, se han optado por soluciones baratas o fabricadas in-house y de sencilla implementación para favorecer un rápido prototipado.


Figura 1: El robot, también conocido como Wheele

El robot, o, como ha sido apodado cariñosamente; Wheele, consta de una Raspberry Pi 3B+ como ordenador de a bordo, que hace de interfaz con la cámara, lee las medidas de los encoders y establece un bus i2c con una IMU mpu-6050. Un microcontrolador ATmega328 de una placa Arduino, comunicado por puerto serie con la Raspberry, ejecuta un PI y actúa sobre los motores. Todo el sistema, exceptuándo el control de bajo nivel del micro, corre en ROS Kinetic, en una configuración de multi-masters que relega los procesos computacionalmente costosos (algoritmos de SLAM, data fusion...) a un portátil conectado a la Raspberry a través de una red wireless dedicada. Como drivers para los motores se han usado tres circuitos integrados L293D (dos puentes H por cada chip), que reciben como input una señal generada por el micro mediante Pulse-Width Modulation. En la sección de hardware de este mismo documento se detallan en más profundidad los sistemas electrónicos empleados, los buses de comunicaciones y se discute la estructura del robot.
La odometría del robot se obtiene a partir de una estimación de la posición a partir de encoders ópticos, y de la velocidad y aceleración medidas por la IMU. La fusión sensorial se realiza con un filtro de Kalman extendido, implementado en el paquete robot localization de ROS. El código desarollado para este proyecto y el uso de software externo es expuesto en la seccion4.
Las imágenes y medidas de profundidad utilizadas para las técnicas SLAM provienen de una Kinect for Xbox 360 de Microsoft, que cuenta con una cámara RGB y un sensor de profundidad matricial. Una breve explicación teórica de las metodologías SLAM empleadas puede encontrarse en la sección5.

## 2. Hardware empleado en el proyecto

Con el fin de obtener una vista general de todo el proyecto, así como del coste del mismo se lista a continuación todos los componentes del robot y su coste:

Chasis del vehículo. Fabricado a partir de un tablón plano de edf cortado en una cnc láser de forma gratuita gracias al Fablab de la Universidad de Sevilla en la facultad de Arquitectura.

- 3-

4 | 2.1 | Estructura

Motores de corriente continua( 1pavos). Adquiridos a través de tiendas digitales por un módico precio, lo cual se refleja en una calidad más bien pésima. Sin embargo, formaban parte de un kit que incluye ruedas y acople al eje de transmisión, suponiendo un ahorro importante de tiempo y dinero.

Encoders ópticos ( 6pavos). Compuestos por un diodo emisor de luz comprados también a través de internet y por un disco que interrumpe el paso del haz lumínico diseñado específicamente e impreso en 3D.

Microcontrolador ATmega328 ( 10pavos). Aunque la gran parte del código implementado en el micro no utiliza las librerías de arduino, por comodidad se ha optado por un microchip ya montado en una placa tipo arduino (un modelo no oficial, clónico).

IMU mpu-6050 ( 2pavos).

Raspberry Pi 3B+ ( 30pavos). Constituye el cerebro del robot, y centraliza la comunicación con los demás sistemas. Aunque puede resultar el componente más caro del proyecto, se disponían de varias de antemano, por lo que no hubo que asumir su coste.

Kinect for Xbox 360 de Microsoft ( 15pavos). Esta popular cámara merece la fama que tiene por lo asequible que es (especialmente el modelo más antiguo) y las utilidades que trae. Se demuestra como la opción más socorrida para desarollar con poco presupuesto aplicaciones que requieran de imágenes o sensores de profundidad.

### 2.1. Estructura

El robot ha sido diseñado con una topología inspirada en los vehículos de exploración espacial conocidos como rovers, utilizando materiales y métodos de construcción asequibles y manteniendo como objetivo una sencilla sustitución e iterabilidad de cada componente. La estructura está diseñada en Free-Cad y compuesta por piezas de madera mecanizadas en una cortadora láser cnc. Algunos elementos sin funcionalidad estructural, como los encoders o el soporte de la cámara, han sido fabricados mediante impresión 3D.

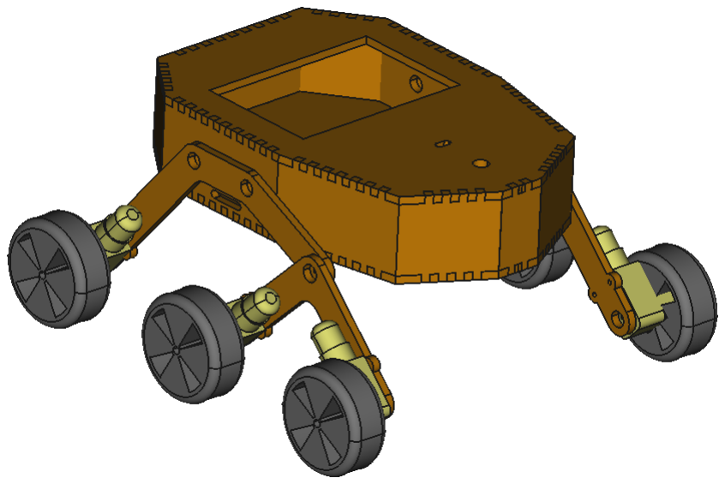
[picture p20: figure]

Figura 2: Modelo CAD del robot

La disposición geométrica es la de un vehículo diferencial, con tres pares de ruedas, cada una con su respectiva pareja de motor y encoder.

- 4-

2.2 | Diseño PCB | 5

### 2.2. Diseño PCB

### 2.3. Controladores de abordo

### 2.3.1. Raspberry Pi

### 2.3.2. Arduino

### 2.4. Cámaras empleadas

- 5-

6

## 3. Software empleado en el proyecto

### 3.1. ROS

ROS (Robotic Operating System) consite en un framework para la robótica sobre el que desarrolladores de cualquier ambito pueden aportar soluciones modulares a los sistemas de forma general. La modularidad de ROS hace que desarrollar un nuevo sistema o prototipo pueda ser una tarea tan sencilla como interconectar módulos de otros desarrolladores con los propios.
Esta característica lo hace idoneo para un proyecto como este en el que el uso de técnicas de percepción, mapeado, localization, etc, complejas se escapa del alcance; y solo sea necesario el desarrollo de modulos específicos de este robot que sean capaces de comunicarse con aquellos más complejos y sean capaces de proporcionarle los datos necesarios para implementar los algoritmos de SLAM.

### 3.1.1. Computación distribuida con ROS-Multimaster Package

Las técnicas de SLAM a testear en el robot desarrollado son computacionalmente costosas. De manera genérica a los metodos de SLAM visual usados, para cada frame capturado por la camara el algoritmo extrae ‘features’ de la imagen, las alamacena y compara los conjuntos con los de otro frame. Entre ambos frames el algoritmo calcula una matriz de transformación homogenea con la cual se es capaz de saber, al menos localmente, cuanto y como se ha desplazado el robot. Sumado a eso cada algoritmo tiene su forma propia de localizar globalmente en el mapa creado al robot. Todo este coste computacional es imposible asumirlo desde una Raspberry-Pi, por lo que surge la necesidad de hacer el procesado en un servidor remoto al robot en tiempo real con las dificultades que eso conlleva, entre ellas y la mas importante, la sincronización de datos.
Bajo estas condiciones de diseño y restricciones aparece una solución de la comunidad: ROS multimaster_fkie. La premisa que lo rige es simple, dado un sistema mutirobot cada elemento mantiene la ejecución de 2 nodos locales, master_discovery y master_sync; el primero es el encargado de mantener una lista del resto de roscores disponibles en la red y de publicar el suyo propio como activo. El otro es el encargado de suscribir su core los nodos de otros cores.
Des esta forma todos tienen acceso de una forma hasta cierto punto ‘real-time’ a los recursos del resto.

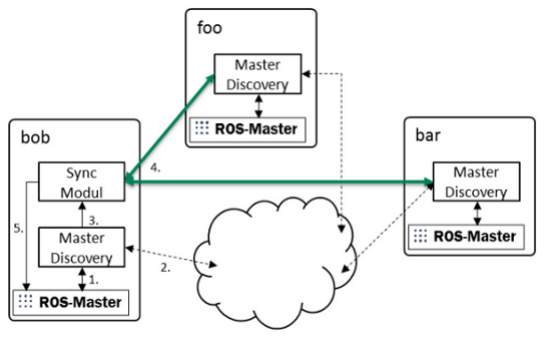
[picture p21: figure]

Figura 3: Esquema del funncionamiento básico del paquete Multimaster

En este proyecto su integración se ha llevado a cabo lanzando en la Raspberry-Pi y en otro PC los nodos correspondientes siendo la Raspberry-Pi la suministradora de información y el PC el encargado de procesarla.

### 3.1.2. Interfaz con IMU

Qué hace, como se procesan los datos y que se publica.

- 6-

3.2 | Implementación filtro estadístico | 7

### 3.1.3. Interfaz con encoders

Mismito que lo de la IMU

### 3.1.4. Odometría

Explicar qué se hace, qué y donde se publica y a quién se suscribe

### 3.1.5. Interfaz Raspberry-Pi/Arduino

Qué hace, a quién se suscribe y donde publica el qué

### 3.1.6. Interfaz Arduino/Motores

Same old same old

### 3.2. Implementación filtro estadístico

Introducción de porqué es interesante y eso, lo de vender la moto as usual

### 3.2.1. Filtro de Kalman Extendido

Background teorico que coma espacio, poner la imagen del filtro esa con colores bonicos y eso

### 3.2.2. ROS-Robot Localization Package

pues eso, lo mismo de lo otro, como funca y tal

### 3.3. Arquitectura general del sistema

Aqui lo de rqt_plot and eso

- 7-

8

## 4. Introducción al SLAM(Simultaneous Localization and Mapping)

¿Qué cojones es el SLAM?

### 4.1. Clasificación técnicas de SLAM

La forma en que se toma información de las imagenes que recibe y de su entorno y cómo la procesa permite distinguir las siguientes tipos de sistemas SLAM visual:

Denso vs Disperso
En función de la cantidad de datos tomada de cada imagen, se realizará ésta clasificación. Las técnicas de SLAM disperso sólo emplean una pequeña región de pixeles, cómo pueden ser puntos característicos. Sin embargo, las técnicas densas emplean la mayoría o todos los píxeles de cada frame que reciben.
Debido a que la cantidad y tipo de información que toman son diferentes, el tipo de mapa que se obtendrá también lo es. Con las técnicas de SLAM disperso se obtendrá una nube de puntos que será una representación de los puntos característicos de las escena y se usará sobre todo para hacer un tracking de la pose de la cámara. Por otro lado, un mapa dentro tendrá muchos más detalles y, requerirá de una mucho más elevada carga computacional.

Directo vs Indirecto
En función de cómo las técnicas de SLAM empleen y traten la información que reciben, se podrá clasificar en SLAM directo o indirecto.
El SLAM infirecto, se basa en extraer primero las features de la imagen, puntos característicos, para posteriormente emplearlos para localizarse y contruir el mapa. Para extraer estos puntos caracteristicos existen muchos descriptores: ORB, SIFT, FAST, etc.
En contraste, el SLAM Directo,emplean directamente la intensidad de los pixeles, de tal modo que se obtengan features intermedios. Estos metodos tratan de obtener la profundidad y estructura del entorno a partir de una optimización del mapa. Los procesos de extracción de puntos característicos son mucho más pesados computacionalmente si se trabaja al mismo rate que un slam indirecto. Por último, destacar, que los metodos indirectos de SLAM son más tolerantes a los cambios de iluminación del entorno.

A continuación, se monstarán una comparativa de una serie de técnicas de SLAM:

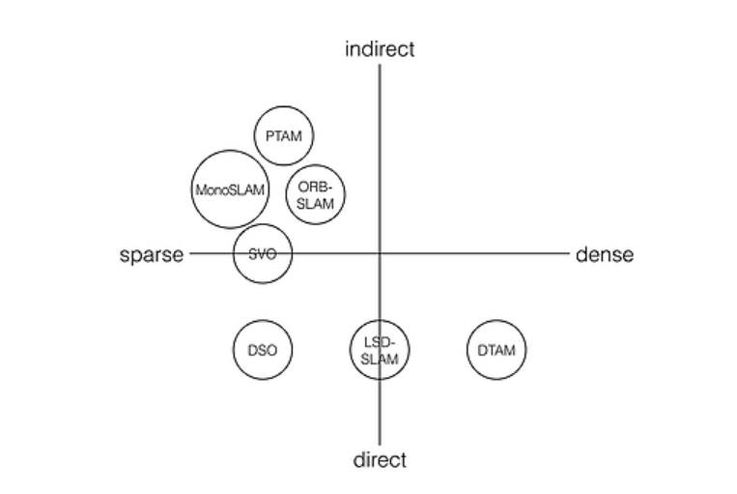
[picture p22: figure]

Figura 4: Comparativa de técnicas SLAM

En éste proyecto, se probará ORB-SLAM2 y RTAB-Map, los cuales abordan el problema del SLAM desde dos puntos de vista completamente distinto, cómo se verá a continuación.

- 8-

4.2 | RTAB-Map SLAM | 9

### 4.2. RTAB-Map SLAM

RTAB-Map (Real-Time Appearance-Based Mapping) es una técnica de Graph-SLAM¹ basada en la detección de bucles cerrados incrementales. Es totalmente funcional con sensores RGB-D, Stereo y LI-DAR.
El detector de bucles cerrados se basará en la comparativa de cuán semenjantes son la imagenes en una localización y la previa. Cuándo una hipótesis de bucle cerrado es aceptada, se añade una nueva restricción al graph del mapa y, tras ello, el optimizador minimiza el error del mapa.

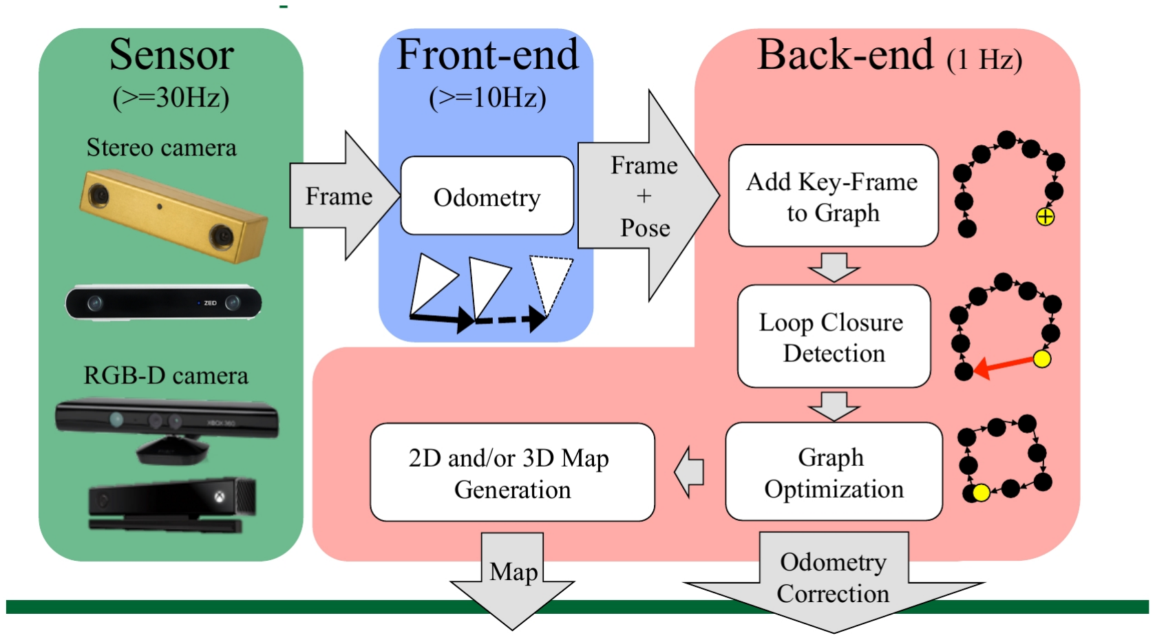
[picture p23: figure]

Figura 5: Esquema del Back-End y Front-End de RTAB-Map

### 4.2.1. Fundamento teórico de la técnica

Este algoritmo plantea una estrategia de particionado de memoria que pretende asemejarse al funcionamiento de la memoria humana, dónde ésta se estructura en:
Memoria de trabajo del robot (Working Memory), la memoria a largo plazo (Long Term Memory), la memoria a corto plazo (Short-term memory) y la memoria sensorial (Sensory Memory).
De ese modo, se mantendrán en la memoria de trabajo del robot aquellas localizaciones que se han visitado recientemente y con más frecuencia, mientras que el resto pasarán a la memoria de largo plazo.

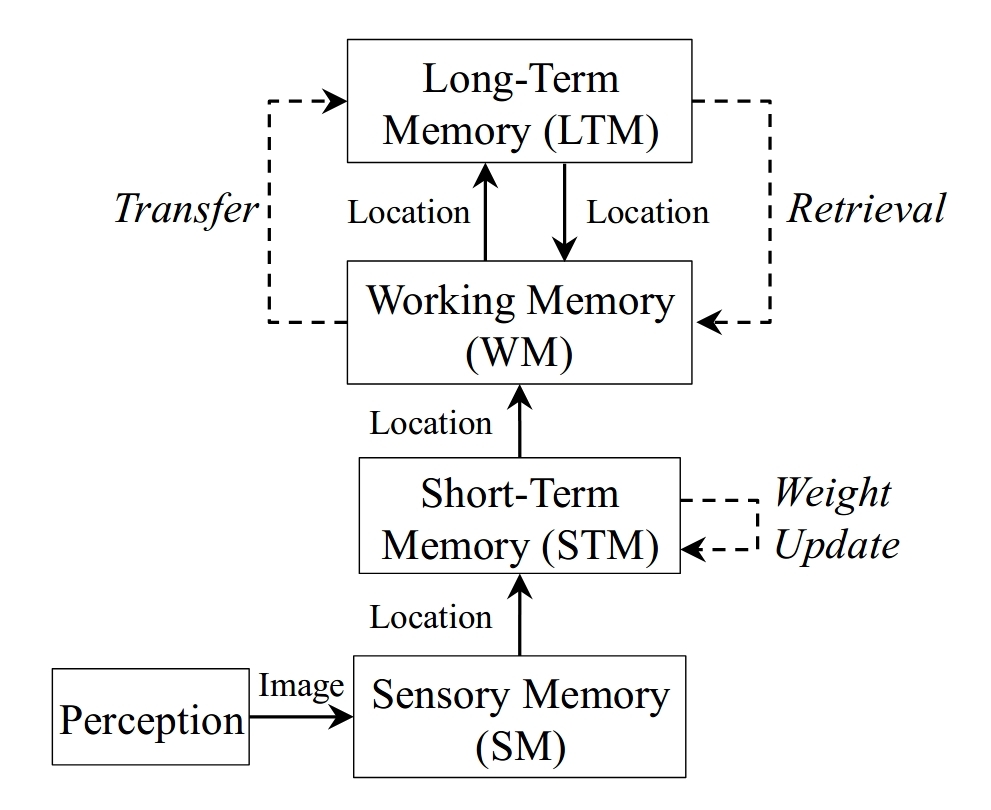
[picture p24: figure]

Figura 6: Estructura de memoria de la técnica RTAB-Map

Se partirá de la premisa de que aquellas localizaciones que son visitadas de forma más frecuente son más propensas a crear bucles cerrados. Por ello, el número de veces que una localización sea visitada será

1http://robots.stanford.edu/papers/thrun.graphslam.pdf

- 9-

10 | 4.2 | RTAB-Map SLAM

empleado como peso, de esta forma serán transferidas desde la memoria de trabajo a la memoria de largo plazo aquellas observaciones que tengan mayor peso.
La memoria a corto plazo, STM, tiene como misión buscar las similitudes que existan entre dos imágenes consecutivas, mientras que la memoria de trabajo, WM, es la encargada de detectar los bucles cerrados entre las localizaciones en el espacio. El número de localizaciones almacenadas en la memoria del trabajo del robot es limitado. El tamaño de la memoria a corto plazo, STM, está basado en la velocidad del robot y en la frecuencia de adquisición de las localizaciones.

### 4.2.2. Análisis de resultados obtenidos

- 10-

4.3 | ORB-SLAM 2 | 11

### 4.3. ORB-SLAM 2

ORB-SLAM2 es una técnica de SLAM en tiempo real para cámaras Monocular, Stereo y RGB-D que se engloba dentro de las técnicas de Sparse-Slam. Se computa la trayectoria y hace una reconstrucción dispersa 3D del entorno. Al igual que todas las técnicas de SLAM, se basa en la detección de bucles cerrados y se relocaliza en tiempo real.
Se basa en la detección de keyframes que emplea para hacer un tracking de los mismos y a partir de ello crear el mapa local que, posteriormente, se optimizará junto al mapa global.
Unos de los puntos destacables de ésta técnica de SLAM son los siguientes:

Emplea grafo de covisibilidad. Tanto el seguimiento como el mapping se focalizan en el área covisible, independientemente del tamaño del mapa completo, consiguiendo así explorar entornos amplios sin aumentar el tiempo y la carga de computación.

La estrategia para detectar los bucles cerrados de visión en tiempo real se basa en la optimización de un de grafo denominado Essencial Graph, lo cuál se desarrollará mas adelante.

### 4.3.1. Fundamento teórico de la técnica

A continuación, se tratará un poco el funcionamiento interno del algoritmo, el cuál presenta el siguiente esquema:

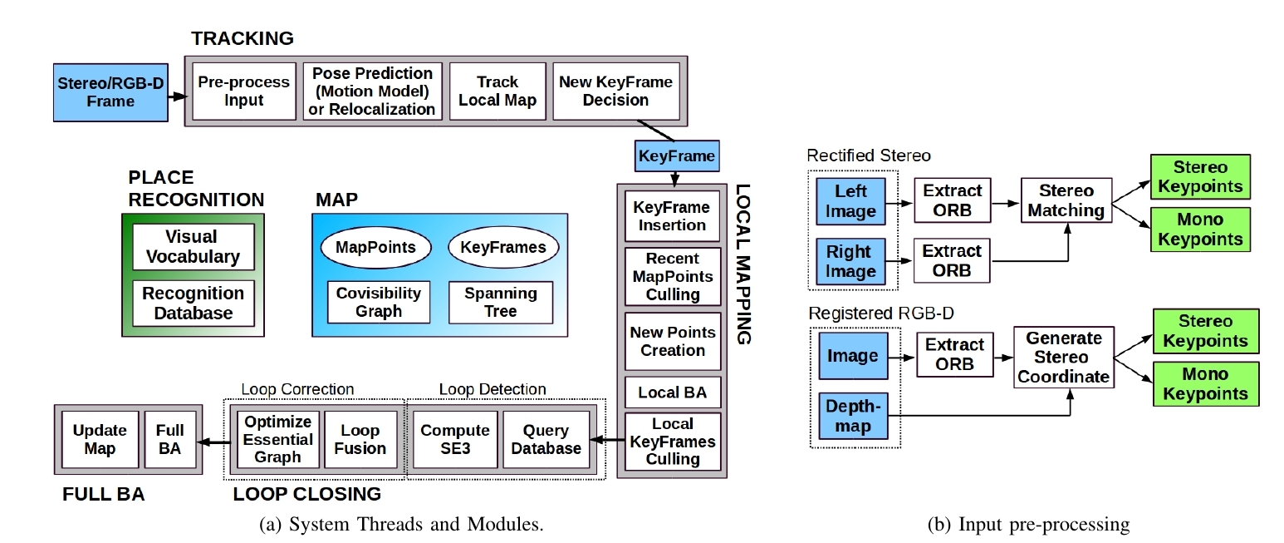
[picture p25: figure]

Figura 7: Estructura interna de ORB-SLAM2

Se observa cómo existen 6 grandes módulos, los cuales de lanzarán en 3 hilos paralelos.
En primer lugar, se tendrá el preprocesamiento de la imagen, de la cuál se obtendrán ORB features (Oriented Fast and Rotated BRIEF).
Los hilos desempeñarán las siguientes funciones:

El tracking se encargará de localizar la cámara en cada frame buscando marches entre las features del mapa local y minimizando la reprojección del error aplicando un Bundle Adjustment ²
sólo de
movimiento.

El Local Mapping se encargará de gestionar y optimizar el mapa local aplicando un BA local.

El hilo de Loop Closing se encargará de detectar bucles cerrados grandes y corregir la deriva acumulada realizando una optimización del grafo del pose obtenido. Este hilo, lanza 4 hilos internos que se encagarán de realizar un Bundle Adjustement completo tras la optimización del grafo del pose, para hayar la solución más optima.

2https://homes.cs.washington.edu/ sagarwal/bal.pdf

- 11-

12 | 4.3 | ORB-SLAM 2

En caso de que el sistema pierda el tracking, lleva integrado un modulo de Plane recognition basado en un vocabulario de palabras que básicamente es una especie de preentrenamiento de la técnica, para poder obtener y asociar keyframes más fácilmente.

### 4.3.2. Análisis de resultados obtenidos

En la imagen a continuación, puede observarse la técnica corriendo en un ordenador. Destacar que ésta técnica de SLAM presenta una carga computacional bastante elevada.

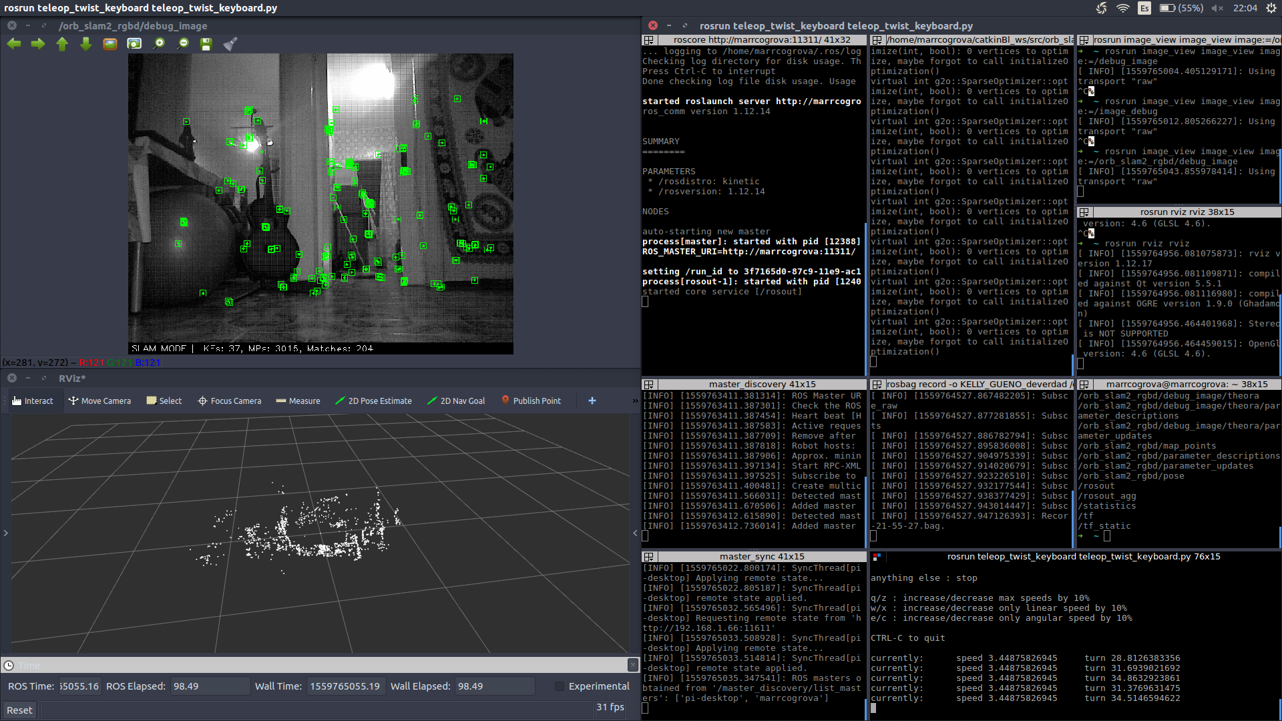
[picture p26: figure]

Figura 8: ORB-SLAM2 en funcionamiento

Se observa en la imagen superior izquierda las features que está obteniendo en ese frame, a partir de las cuales se ha creado en mapa local y, por extensión el global. En la imagen inferior izquierda, se puede observar el mapa creado, el cuál se analizará más tarde.
Por último, a la derecha se tienen las terminales a partir de las cuales se ha lanzado el SLAM y se realiza la comunicación con el robot.
- 12-

REFERENCIAS | 13

## Referencias

[1] R. Mur-Artal and J. D. Tardós, “ORB-SLAM2: an open-source SLAM system for monocular, stereo and RGB-D cameras,” IEEE Transactions on Robotics, vol. 33, no. 5, pp. 1255–1262, 2017.
[2] IntRoLab, “RTAB-Map(real-time appearance-based mapping): RGB-D, stereo and lidar graph-based SLAM.” https://github.com/introlab/rtabmap, 2014.
[3] T. Moore and D. Stouch, “A generalized extended kalman filter implementation for the robot operating system,” in Proceedings of the 13th International Conference on Intelligent Autonomous Systems (IAS-13), Springer, July 2014.
[4] M. Harms, “Python interface for cmdmessenger arduino serial communication library.” https://github.com/harmsm/PyCmdMessenger, February 2017.
[5] T. Elenbaas, “Command messenger communication library for arduino & .NET.” https://github.com/thijse/Arduino-CmdMessenger, (https://github.com/thijse/Arduino-CmdMessenger) September 2017.
[6] “Gammon software solutions.” http://www.gammon.com.au.
[7] Atmel, Atmel ATmega640 Datasheet, February 2014.
- 13-

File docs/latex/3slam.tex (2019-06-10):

\section{Análisis e introducción a las técnicas de SLAM}
El SLAM\textit{(Simultaneous Localization and Mapping)} es una técnica cuyo objetivo es contruir un mapa de un entorno desconocido con un robot móvil 
y conocer la posición de dicho robot dentro del mapa. \\
El primer planteamiento de la resolución de estos dos problemas como son la localización de un robot y la creación de mapas de manera conjunta surgió 
en 1986 en un congreso del IEEE en San Francisco. \\
Durante aquellos años, se había comenzado a introducir métodos probabilístico en la inteligencia artificial 
y en la robótica. En dicha conferencia, se llegó a la conclusión de que la generación de mapas consistentes y la localización de manera probabilistica era
un problema fundamental.\\

Tras ello, se establecieron las bases estadisticas para describir la relaciones entre \textit{landmarks}, objetos de referencia y 
para manipular la incertidumbre geométrica. \\
El planteamiento básico del problema de SLAM es el mostrado a continuación:
\begin{figure}[h!]
    \centering
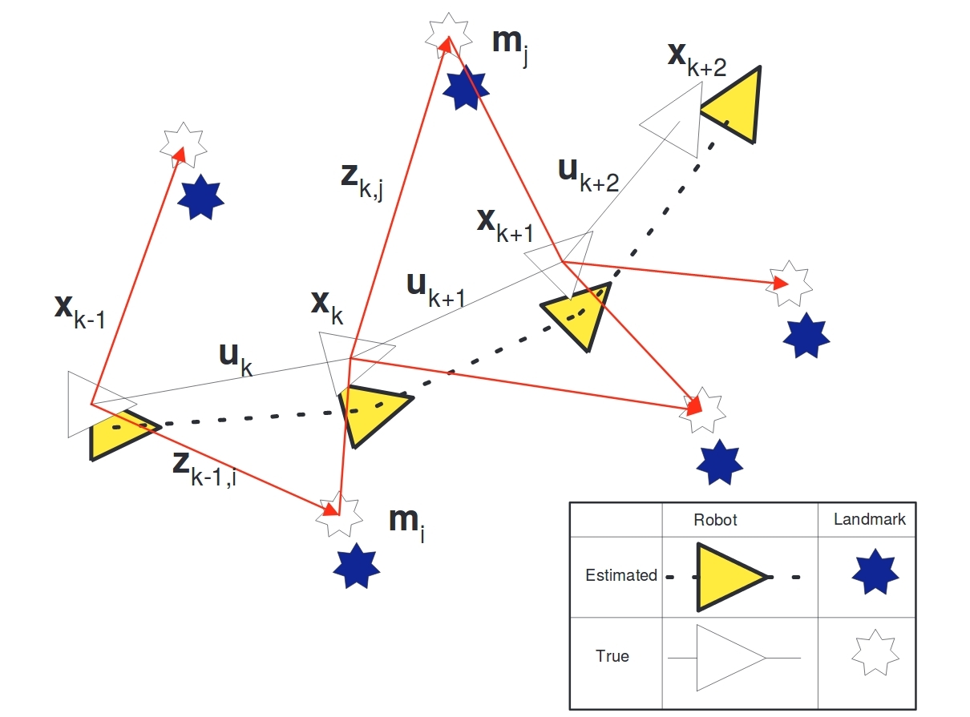
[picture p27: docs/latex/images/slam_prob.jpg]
    
    \caption{Problema básico de SLAM}
\end{figure}

Dado un robot que se mueve por un entorno desconocido, tomando observaciones relativas de un número desconocido de landmarks empleando un sensor posicionado
en el robot; para el instante \textit{k}, se definen las siguientes variables:
\begin{itemize}
    \item $\textbf{x}_k$: Vector de estados que describe la posición y orientación del vehículo.
    \item $\textbf{u}_k$: Vector de control aplicado el instante anterior sobre el vehículo para que se encuentre
en el estado $\textit{x}_k$ en el instante \textit{k}.
    \item $\textbf{m}_i$:Vector que describe la posición del i-ésimo landmark cuya verdadera ubicación se supone invariable con el tiempo.
    \item $\textbf{z}_{ik}$: Observación tomada desde el vehiculo de la posición del i-ésimo landmark en el instante \textit{k}.
\end{itemize}
Por tanto, se deberá computar la siguiente distribución probabilística en cada instante \textit{k}:
\begin{equation}
    P\Big( \textbf{x}_k ,m | \textbf{Z}_{0:k},\textbf{U}_{0:k},x_0\Big)
\end{equation}
La solución se obtendrá de manera recursiva empleando el teorema de Bayes en un proceso en dos pasos: \textit{Time-Update} y \textit{Measurement-Update}. Para ello,
será necesario conocer el modelo de observación y el de movimiento. \\

\begin{center}
    $P\Big( \textbf{z}_k | \textbf{x}_{k},m \Big)$ \hspace{2cm} $P\Big( \textbf{x}_k | \textbf{x}_{k-1},\textbf{u}_{k} \Big)$
\end{center}

Una vez planteado de manera superficial el problema a resolver, el modo de abordarlo se ha desarrollado en muchas direcciones durante los últimos 20 años. \\
Algunos de estos métodos se muestran a continuación y se hablará de ellos, para posteriormente indagar en dos técnicas concretas.
\subsection{Clasificación técnicas de SLAM}
La forma en que se toma información de las imágenes que recibe y de su entorno y como la procesa permite distinguir los siguientes tipos de sistemas
SLAM visual:
\begin{itemize}
\item \textit{Denso vs Disperso} \\
En función de la cantidad de datos tomada de cada imagen, se realizará esta clasificación. Las técnicas de SLAM disperso sólo emplean una pequeña
región de píxeles, como pueden ser puntos característicos. \\
Sin embargo, las técnicas densas emplean la mayoría o todos los píxeles de cada frame que reciben. \\

Debido a que la cantidad y tipo de información que toman son diferentes, el tipo de mapa que se obtendrá también lo es. Con las técnicas de SLAM
disperso se obtendrá una nube de puntos que será una representación de los puntos característicos de las escena y se usará sobre todo para hacer
un tracking de la pose de la cámara. Por otro lado, un mapa denso tendrá muchos más detalles y, requerirá una carga computacional más elevada.

 \item \textit{Directo vs Indirecto} \\
En función de como las técnicas de SLAM empleen y traten la información que reciben, se podrá clasificar en SLAM directo o indirecto.\\
El SLAM Indirecto, se basa en extraer primero las features de la imagen, puntos característicos, para posteriormente emplearlos para localizarse y contruir
el mapa. Para extraer estos puntos característicos existen muchos descriptores: ORB, SIFT, FAST, etc. \\

En contraste, el SLAM Directo, emplea directamente la intensidad de los píxeles, de tal modo que se obtengan features intermedios. Estos métodos tratan de 
obtener la profundidad y estructura del entorno a partir de una optimización del mapa. Los procesos de extracción de puntos característicos son mucho más
pesados computacionalmente si se trabaja al mismo rate que un slam indirecto.\\
Por último, destacar, que los métodos indirectos de SLAM son más tolerantes a los cambios de iluminación del entorno.\\

A continuación, se mostrará una comparativa de una serie de técnicas de SLAM:
\begin{figure}[h!]
    \centering
    
    \caption{Comparativa de técnicas SLAM}
\end{figure}

\end{itemize}

\subsection{Técnicas SLAM implementadas en este proyecto}
Destacar que, mientras la primera metodología de SLAM es una técnica determinista, la segunda será probabilistica.
\subsubsection{\textit{RTAB-Map SLAM}}
RTAB-Map \textit{(Real-Time Appearance-Based Mapping)} es una técnica de Graph-SLAM \footnote{http://robots.stanford.edu/papers/thrun.graphslam.pdf} basada en la detección de bucles cerrados incrementales. Es totalmente funcional 
con sensores RGB-D, Stereo y LIDAR. \\
El detector de bucles cerrados se basará en la comparativa de cuán semenjantes son la imágenes en una localización y la previa. Cuándo una hipótesis 
de bucle cerrado es aceptada, se añade una nueva restricción al \textit{graph} del mapa y, tras ello, el optimizador minimiza el error del mapa. \\

\begin{figure}[h!]
    \centering
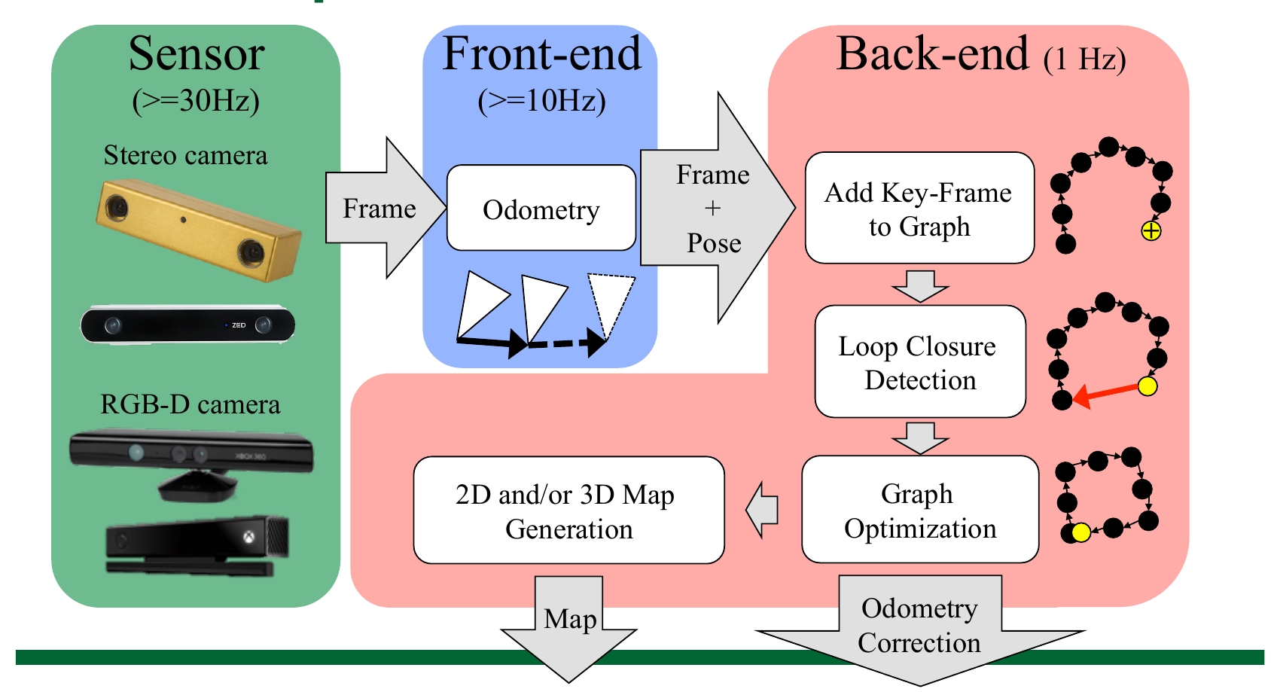
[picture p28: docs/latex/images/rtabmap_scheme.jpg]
    
    \caption{Esquema del Back-End y Front-End de RTAB-Map}
\end{figure}

Este algoritmo plantea una estrategia de particionado de memoria que pretende asemejarse al funcionamiento de la memoria humana, 
donde esta se estructura en: \\
Memoria de trabajo del robot \textit{(Working Memory)}, memoria a largo plazo \textit{(Long Term Memory)}, 
memoria a corto plazo \textit{(Short-term memory)} y memoria sensorial \textit{(Sensory Memory)}. \\
De ese modo, se mantendrán en la memoria de trabajo del robot aquellas localizaciones que se han visitado recientemente 
y con más frecuencia, mientras que el resto pasarán a la memoria de largo plazo. \\

\begin{figure}[h!]
    \centering
    
    \caption{Estructura de memoria de la técnica RTAB-Map}
\end{figure}

Se partirá de la premisa de que aquellas localizaciones que son visitadas de forma más frecuente son más propensas a 
crear bucles cerrados. Por ello, el número de veces que una localización sea visitada será empleado como peso, de 
esta forma serán transferidas desde la memoria de trabajo a la memoria de largo plazo aquellas observaciones que 
tengan mayor peso.\\
La memoria a corto plazo, \textit{STM}, tiene como misión buscar las similitudes que existan entre dos imágenes
consecutivas, mientras que la memoria de trabajo, \textit{WM}, es la encargada de detectar los bucles cerrados entre las
localizaciones en el espacio. El número de localizaciones almacenadas en la memoria del trabajo del robot es
limitado. El tamaño de la memoria a corto plazo, \textit{STM}, está basado en la velocidad del robot y en la frecuencia de
adquisición de las localizaciones. \\

% NO SE SI METER ESTA PARTE
\begin{comment}
Es importante destacar que todas las observaciones almacenadas en la memoria a largo plazo, \textit{STM}, del robot no se
usan para detectar bucles cerrados. No obstante, es importante elegir cuidadosamente las localizaciones que se
almacenan en esta memoria. Almacenar las observaciones según la técnica FIFO (First In First Out), sería un
error debido a que, como el algoritmo establece un número máximo de localizaciones que se pueden
almacenar mientras se está explorando un entorno, podríamos alcanzar el superar el umbral de tiempo
establecido sin llegar a cerrar el bucle haciendo que las localizaciones más antiguas nunca consigan asociarse. \\
como alternativa, el orden de almacenamiento de las observaciones se elige de forma aleatoria, aunque es
preferible mantener en la memoria de trabajo aquellas localizaciones que son más susceptibles de ser
observadas.
\end{comment}
\subsection{Framework de optimización Octomap}
El paquete de ROS empleado para emplear la ténica RTAB-Map,\textit{rtabmap-ros}, posee la posibilidad de extraer también el mapa de ocupación 2D y 3D gracias al Framework 
\textit{Octomap}\footnote{https://octomap.github.io/}. \\
Este framework es una librería de C++ que permite la obtención de mapas probabilísticos basándose en una estructura de representación jerárquica de datos para subdividir
el espacio 3D, esta estructura es denominada \textit{Octotrees}. \\

\begin{figure}[h!]
    \centering
    
    \caption{Optimización realizará empleando los \textit{Octotrees}}
\end{figure}

Los \textit{Octotrees} se emplean para almacenar propiedades booleanas del entorno, en el caso de
la robótica estas propiedas booleanas es la ocupación de dicha celda, de la cual es posible definir su tamaño mínimo en función de la resolución de mapa
deseada.
\begin{figure}[h!]
    \centering
    
    \caption{Funcionamiento del \textit{octotree} y su estructura en árbol}
\end{figure}

\newpage
\subsubsection{\textit{ORB-SLAM 2}}
ORB-SLAM2 es una técnica de SLAM en tiempo real para cámaras Monocular, Stereo y RGB-D que se engloba dentro de las técnicas de 
\textit{Sparse-Slam}. Se computa la trayectoria y hace una reconstrucción dispersa 3D del entorno. Al igual que todas las técnicas 
de SLAM, se basa en la detección de bucles cerrados y  se relocaliza en tiempo real. \\
Se basa en la detección de \textit{keyframes} que emplea para hacer un tracking de los mismos y a partir de ello crear el 
mapa local que, posteriormente, se optimizará junto al mapa global. \\
Unos de los puntos destacables de esta técnica de SLAM son los siguientes:
\begin{itemize}
    \item Emplea \textit{grafo de covisibilidad}. Tanto el seguimiento como el mapping se focalizan en el área covisible,
    independientemente del tamaño del mapa completo, consiguiendo así explorar entornos amplios sin
    aumentar el tiempo y la carga de computación.

    \item La estrategia para detectar los bucles cerrados de visión en tiempo real se basa en la optimización de
   un de grafo denominado \textit{Essencial Graph}, lo cuál se desarrollará mas adelante.
\end{itemize}

A continuación, se tratará un poco el funcionamiento interno del algoritmo, el cuál presenta el siguiente esquema:
\begin{figure}[h!]
    \centering
    
    \caption{Estructura interna de ORB-SLAM2}
\end{figure}

Se observa como existen 6 grandes módulos, los cuales de lanzarán en 3 hilos paralelos. \\
En primer lugar, se tendrá el preprocesamiento de la imagen, de la cuál se obtendrán  ORB features 
\textit{(Oriented Fast and Rotated BRIEF)}. \\
Los hilos desempeñarán las siguientes funciones:
\begin{itemize}
    \item El \textit{tracking} se encargará de localizar la cámara en cada frame buscando marches entre las features
    del mapa local y minimizando la reprojección del error aplicando un \textit{Bundle Adjustment}\footnote{https://homes.cs.washington.edu/~sagarwal/bal.pdf} sólo de 
    movimiento.
    \item El \textit{Local Mapping} se encargará de gestionar y optimizar el mapa local aplicando un \textit{BA} local.
    \item El hilo de \textit{Loop Closing} se encargará de detectar bucles cerrados grandes y corregir la deriva acumulada
    realizando una optimización del grafo del \textit{pose} obtenido. Este hilo, lanza 4 hilos internos que se encagarán de
    realizar un \textit{Bundle Adjustement} completo tras la optimización del grafo del \textit{pose}, para hayar la solución
    más optima.
\end{itemize}

En caso de que el sistema pierda el tracking, lleva integrado un modulo de \textit{Plane recognition} basado en un vocabulario 
de palabras que básicamente funciona como un preentrenamiento de la técnica, para poder obtener y asociar keyframes más fácilmente. \\

En la imagen a continuación, puede observarse la técnica corriendo en un ordenador. Destacar que esta técnica de SLAM presenta una carga computacional bastante elevada.
\begin{figure}[h!]
    \centering
    
    \caption{ORB-SLAM2 en funcionamiento}
\end{figure}

Se observa en la imagen superior izquierda las features que está obteniendo en ese frame, a partir de las cuales se ha creado el mapa local y,
por extensión el global. En la imagen inferior izquierda, se puede observar el mapa creado, el cuál se analizará más tarde.\\
Por último, a la derecha se tienen las terminales a partir de las cuales se ha lanzado el SLAM y se realiza la comunicación con el robot.\\

\newpage

\section{Comparativa de resultados empleando \textit{rosbags} del robot}
Para realizar un análisis y una comparativa entre estas dos técnicas de SLAM, se ha optado por generar un set de datos del robot y correrlo con ambas técnicas,
de tal modo que ambas téngan los mismos datos de entrada y se pueda analizar de mejor modo la salida de la arquitectura. \\
Aunque normalmente se correría el robot junto con el SLAM, si no se hubieran grabado estos set de datos sería más complejo comparar estas técnicas. \\
Estos datasets, que han sido grabados en forma de \textit{rosbag}, se grabaron desde el ordenador en el que corre el SLAM, de todos los topicos que se recibian
del ordenador de abordo del robot a través de la comunicación \textit{Multi-master} implementada.\\
A continuación, se muestra una imagen de los topicos contenidos en ambos datasets:
\begin{figure}[h!]
    \centering
    
    \caption{topicos contenidos en el bag}
\end{figure}

En ambos datasets el robot recorrerá un camino en torno al salón de la casa de uno de los integrantes del grupo. En el primer dataset, el estado del salón será 
el comun, de modo que haya una parte del mapa que no contendrán muchas features. Sin embargo, en el segundo se colocaron objetos en zonas donde la cantidad de features
y los contrastes del mapa eran reducidos para así comparar el resultado inicial con uno en un entorno experimental, donde se ha forzado que el entorno esté lleno de features.\\

Se realizarán 3 pruebas, las cuales se encuentras recogidas en vídeos existentes en la carpeta del proyecto. En primer lugar se mostrará el mapa creado por \textit{RTAB-Map} y
la estimación del \textit{path} del robot. Tras ello, se mostrará el mapa de ocupación generado por \textit{OctoMap} tanto en 2D como en 3D y, por último, se mostrará el
resultado obtenido con \textit{ORB-SLAM2 RGB-D}. \\

Destacar que, se pueden observar los resultados de las técnicas de SLAM en el directorio \textit{videos\_wheeleSLAM} de este proyecto.
\newpage

\subsection{Análisis de resultados con el primer \textit{rosbag}}
Este dataset será el que contendrá el salón en un estado comun, sin alterar la cantidad de features existentes en el entorno. \\
En él, se recorrerá un camino de, aproximadamente, 1$m^2$ en torno al salón.

\subsubsection{RTAB-Map y local path}
En primer lugar, se mostrará el mapa denso obtenido gracias a RTABMAP. Se observa como el loop closure del mapa ha funcionado correctamente, de tal modo que la estructura final
del mapa será el rectangulo que confirma el salón.
\begin{figure}[h!]
    \centering
    
    
    \caption{Mapa creado antes y después del \textit{Loop Closure}}
\end{figure}

El mapa obtenido, será un mapa denso el cual posee toda la información posible del entorno, como se muestra a continuación:
\begin{figure}[h!]
    \centering
    
    \caption{Mapa obtenido con RTAB-Map}
\end{figure}

Gracias a la realización de dicho mapa, se ha optado por medir la tela grande de la pared y el cuadro sobre el sillón naranja tanto en el mapa como la distancia real, para comprobar
el error que posee esta técnica.

\begin{center}
\begin{tabular}{ c | c | c | c }
     & Ancho en el mapa creado & Ancho real & Error de RTAB-Map\\
     \hline
     Tela de la pared & 1.72 m & 1.8 m & 0.08 m\\
     Cuadro sobre sillón & 1.07 m & 1.13m & 0.05m\\
\end{tabular}
\end{center}

Se observa como, el error de esta técnica de SLAM frente a las medidas reales es casi un orden de magnitud menor, algo que se considera asumible.

\subsubsection{OctoMap}
Gracias a \textit{Octomap} se ha obtenido el mapa de ocupación probabilístico del entorno. Se mostrará, al igual que antes, el mapa antes y después del loop closure, ya que es lo
destacable de esta técnica de SLAM.
\begin{figure}[h!]
    \centering
    
    
    \caption{Mapa de ocupación antesy despues del \textit{Loop Closure}}
\end{figure}

Además, \textit{Octomap} nos proporciona el mapa de ocupación 3D, como el mostrado a continuación:
\begin{figure}[h!]
    \centering
    
    \caption{Mapa obtenido con RTAB-Map y empleando el framework \textit{Octomap}}
\end{figure}

\subsubsection{ORB-SLAM2 RGB-D}
En el caso del ORB-SLAM2, con este dataset los resultados han sido peores, debido a que en cierto momento, los cambios de iluminosidad procedentes del balcón de la casa, hacen que se
se pierda dentro del mapa creado. A continuación se muestra el frame anterior a la pérdida de la localización dentro del mapa. Los colores representan la altura en el eje Z.
\begin{figure}[h!]
    \centering
    
    \caption{Momento anterior a la pérdida del robot en el primer dataset}
\end{figure}

Sin embargo, se observa como, cuando vuelve a ver el inicio del mapa, donde tomó un número elevado de features, se relocalizará, como se muestra a continuación:
\begin{figure}[h!]
    \centering
    
    \caption{Relocalización del robot en el primer dataset}
\end{figure}

Debido a que el mapa no se ha llegado a completar se ha obtado por no realizar una comparativa de las medidas en este caso.

\newpage

\subsection{Análisis de resultados con el segundo \textit{rosbag}}
En este segundo dataset, el escenario será más parecido a un escenario experimental debido a que se han colocado objetos por el salón de tal modo que en todo el mapa se
obtengan una cantidad elevada de features.

\subsubsection{RTAB-Map y local path}
Al igual que anteriormente, se destacará el loop closure detectado por el mapa. Se observa como, antes de dicho momento, las imágenes de la tela de la pared aparecen superpuestas,
y sin embargo, posteriormente, se puede ver que ha detectado que ya conocia ese setpoint y cerró el bucle:
\begin{figure}[h!]
    \centering
    
    
    \caption{Mapa creado antes y después del \textit{Loop Closure} con el segundo dataset}
\end{figure}

El mapa obtenido, será un mapa denso el cual posee toda la información posible del entorno, como se muestra a continuación:

\begin{figure}[h!]
    \centering
    
    \caption{Mapa obtenido con RTAB-Map empleando el segundo dataset}
\end{figure}
    
\newpage
    \subsubsection{OctoMap}
Gracias a \textit{Octomap} se ha obtenido el mapa de ocupación probabilístico del entorno. Se mostrará, al igual que en las secciones anteriores, el mapa antes y después del loop closure, ya que es lo destacable de esta técnica de SLAM.
\begin{figure}[h!]
    \centering
    
    
    \caption{Mapa de ocupación antes y después del \textit{Loop Closure}}
\end{figure}

Además, \textit{Octomap} nos proporciona el mapa de ocupación 3D, como el mostrado a continuación:
\begin{figure}[h!]
    \centering
    
    \caption{Mapa obtenido con RTAB-Map y empleando el framework \textit{Octomap}}
\end{figure}

\newpage
\subsubsection{ORB-SLAM2 RGB-D}
En este segundo set de datos, se evitó el cambio de iluminación en el punto donde antes se perdió, de tal modo que en este caso no pase y, efectivamente, como se mostrará a continuación, no pasó:
\begin{figure}[h!]
    \centering
    
    \caption{Modificación del entorno para evitar la perdida de ORB}
\end{figure}

Por tanto, en este caso sí se ha logrado obtener un mapa disperso del entorno:
\begin{figure}[h!]
    \centering
    
    \caption{Mapa del entorno empleando ORB-SLAM2}
\end{figure}

Se observa cómo el mapa obtenido empleando esta técnica se basa mayoritariamente en la detección de los features del entorno. En comparativa con RTAB-Map, esta técnica podría parecer
mucho peor, sin embargo, bajo un ordenador de altas prestaciones los resultados para robótica sin muy destacables ya que el mapa disperso es completamente funcional para poder relocalizarse
y, de ese modo, conocer la posición del robot móvil que esté implementando el SLAM en ese momento.
\newpage
\subsection{Resultados obtenidos de ORB-SLAM2 Monocular}
Debido a la compleja inicialización que conlleva emplear esta técnica monocular, no ha sido posible evaluar su funcionamiento con los bags generados, ya que no se logró que se ejecutara correctamente. Sin embargo, para comprobar su funcionamiento, se ha optado por mover la cámara \textit{Hand-handle}, de tal modo que se asegure la inicialización del SLAM. \\
El gran punto a favor que posee el empleo de SLAM monocular es que no es sensible a la luz, de tal modo que funciona correctamente en exteriores. \\
Por ello, la prueba realiza es en el mismo salón, pero saliendo al balcón y grabando al exterior. \\

Para inicializar el SLAM, ha sido necesario asegurarse que se tomaban y se lograban trackear las \textit{features} de la tela de la pared. A continuación, se mostrará una imagen
del mapa grabado durante bastante tiempo; asegurándose de que se tomaban los suficientes puntos característicos, y se intentó realizar una prueba de cómo estima la altura del piso, 
saliendo al balcón y haciendo que la cámara apuntase al suelo. Es por ello que el mapa tiene la siguiente forma:

\begin{figure}[h!]
    \centering
    
    \caption{Mapa del entorno empleando ORB-SLAM2 Monocular Hand-Handle}
\end{figure}

Se observa cómo esta técnica es insensible a los cambios de luminosidad en la imagen anterior, y cómo los puntos alejados que ha tomado son features tomadas de los edificios de enfrente de la
casa.

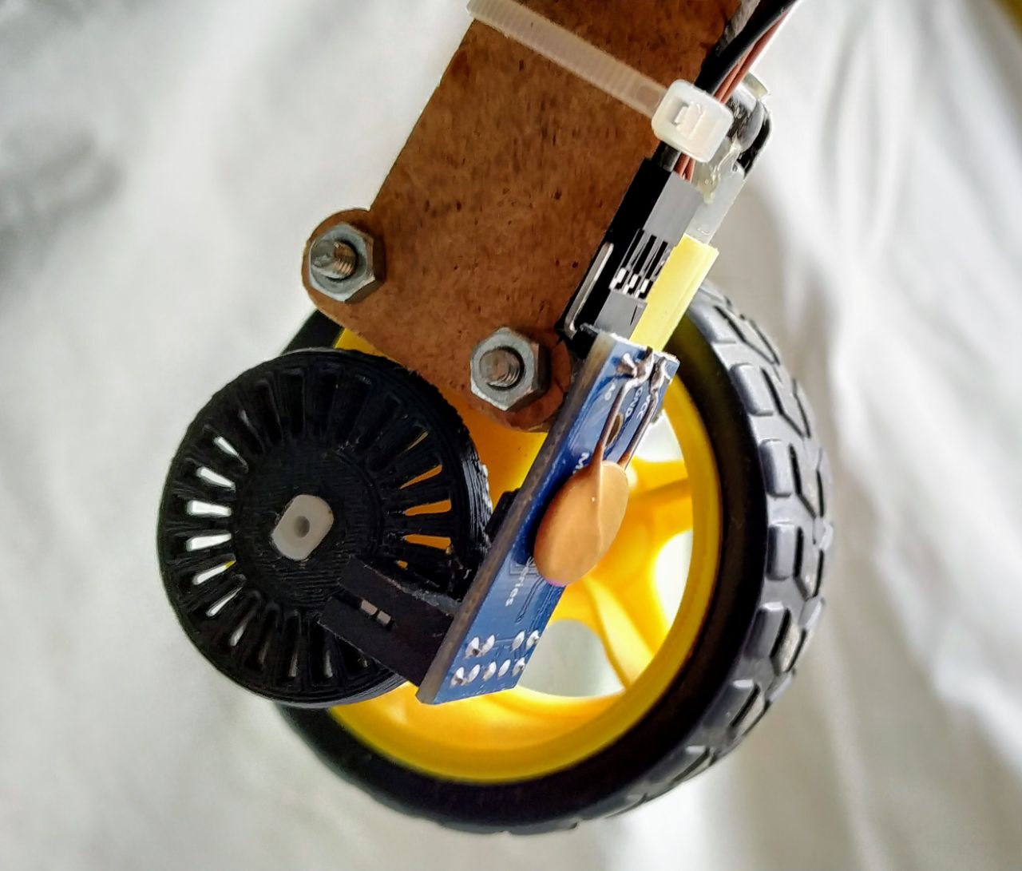
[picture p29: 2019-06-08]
docs/latex/images/hw/encoder_onrobot.jpg

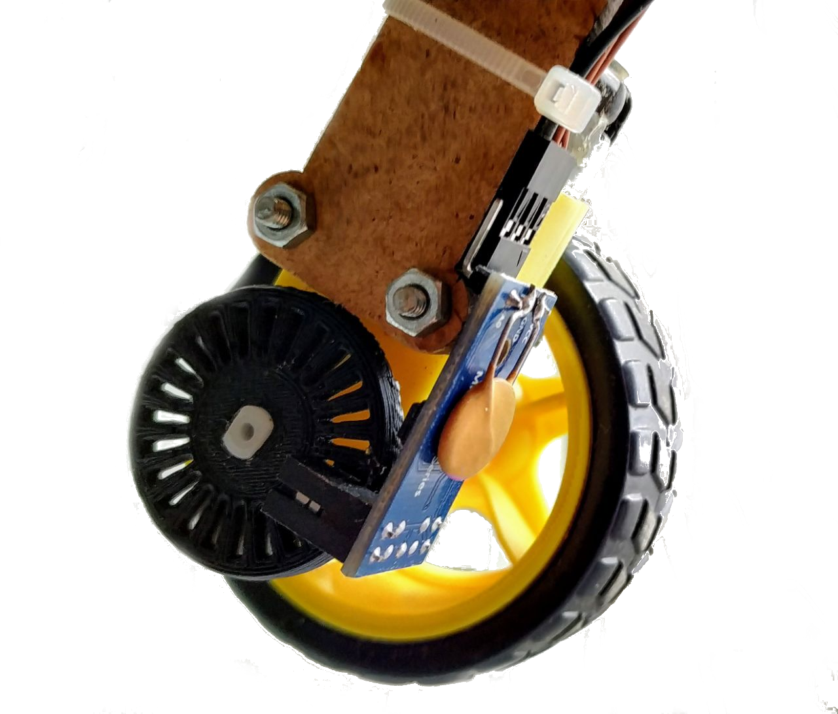
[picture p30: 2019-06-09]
docs/latex/images/hw/rueda.png

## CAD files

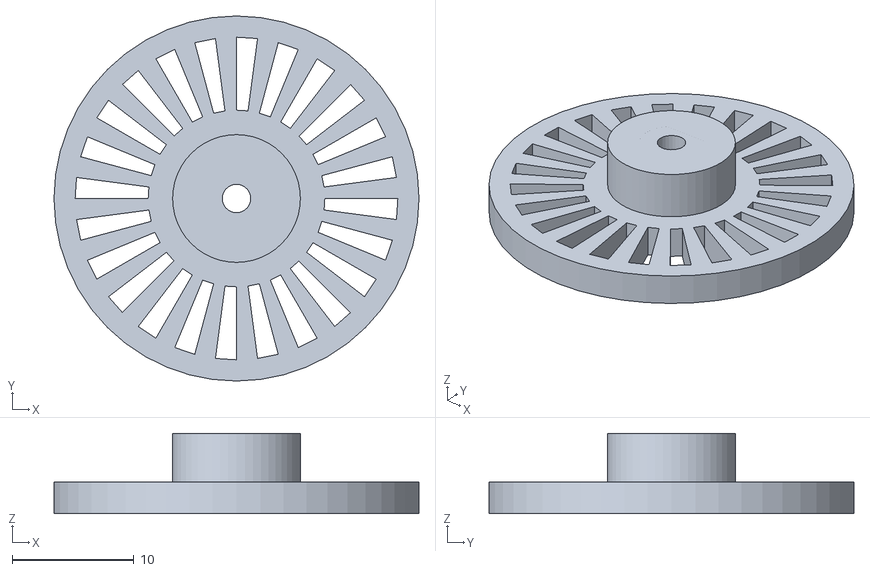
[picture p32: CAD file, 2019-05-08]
Hardware/encoders/enc_mod.stl
30.0 x 30.0 x 6.61

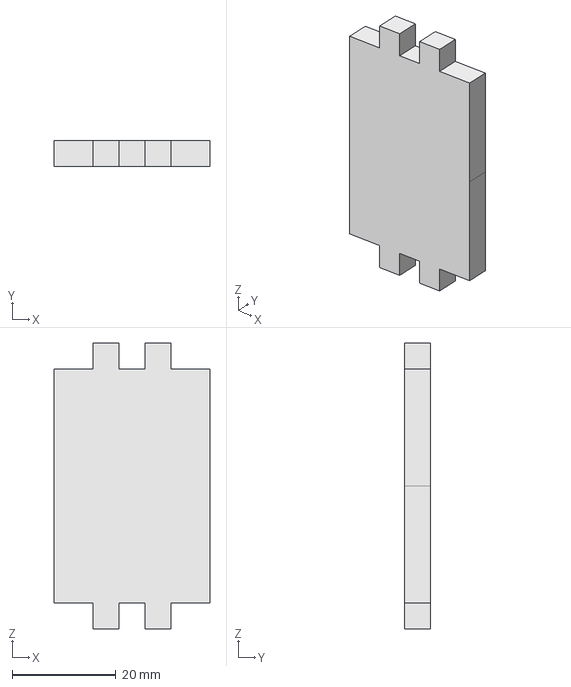
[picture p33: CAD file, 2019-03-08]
Hardware/FreeCad/chasis/face.fcstd
30.0 x 5.00 x 55.0 mm

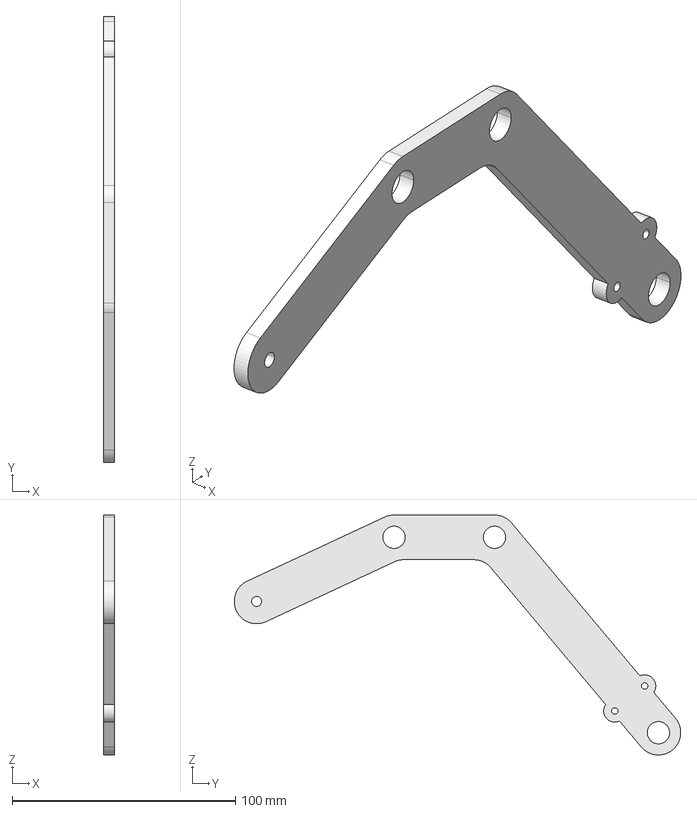
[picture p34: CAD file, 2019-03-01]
Hardware/FreeCad/rocker-bogie/rb_chasis.fcstd
5.00 x 200.0 x 107.5 mm

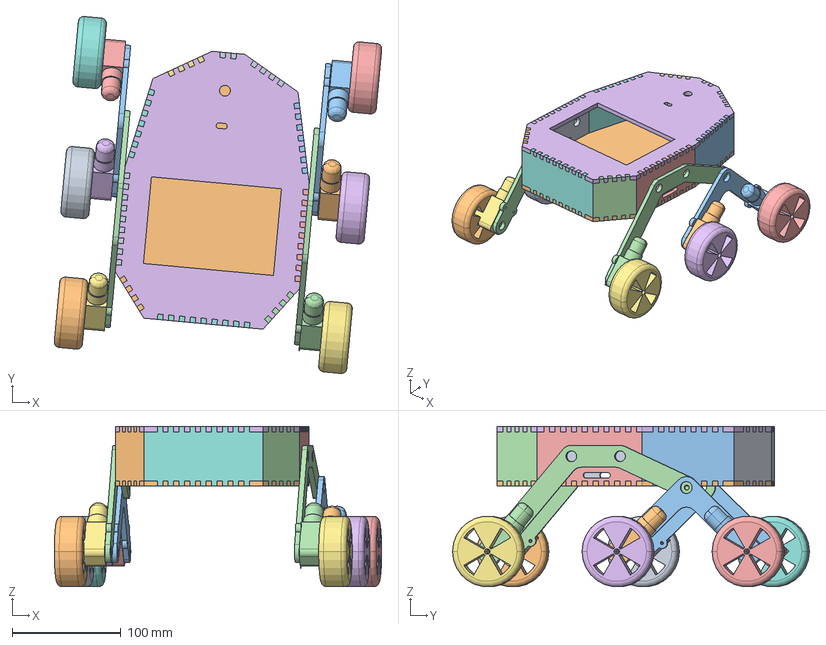
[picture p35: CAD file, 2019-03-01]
Hardware/FreeCad/wheele_assambley.fcstd
300.9 x 328.1 x 147.3 mm
Product1
Product002
Product003
Product004
Product005
Product006
Product007
Product008
Product009
Product010
Product1.1
Product1.002
Product1.003
Product1.004
Product1.005
Product1.006
Product1.007
Product1.008
Product6
Product011
Product015
Product016
Product017
Product018
Product019

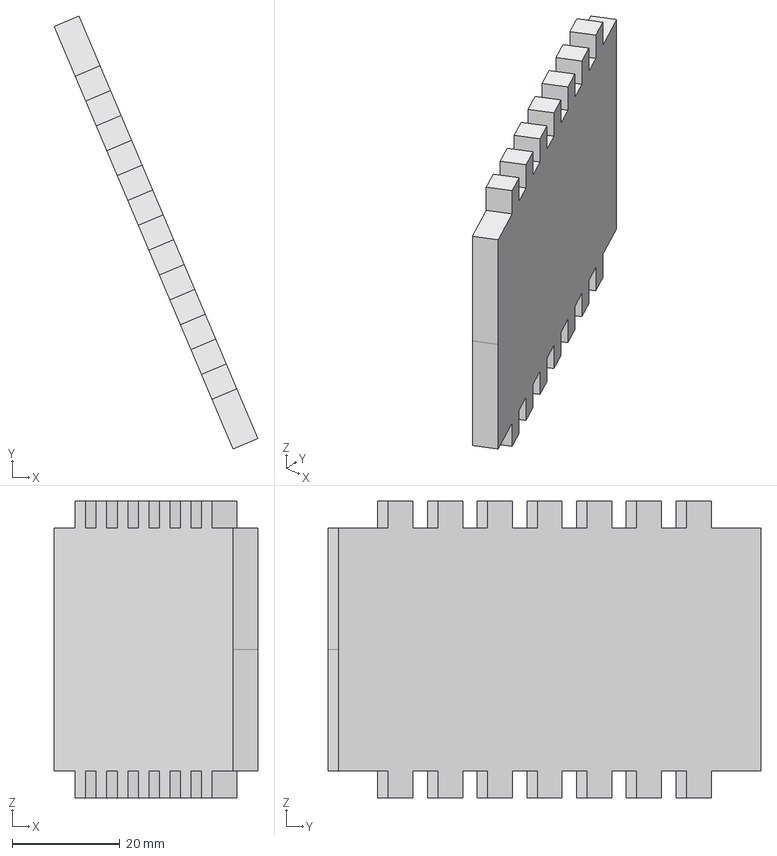
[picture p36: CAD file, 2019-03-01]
Hardware/FreeCad/chasis/front_sides.fcstd
37.7 x 80.2 x 55.0 mm

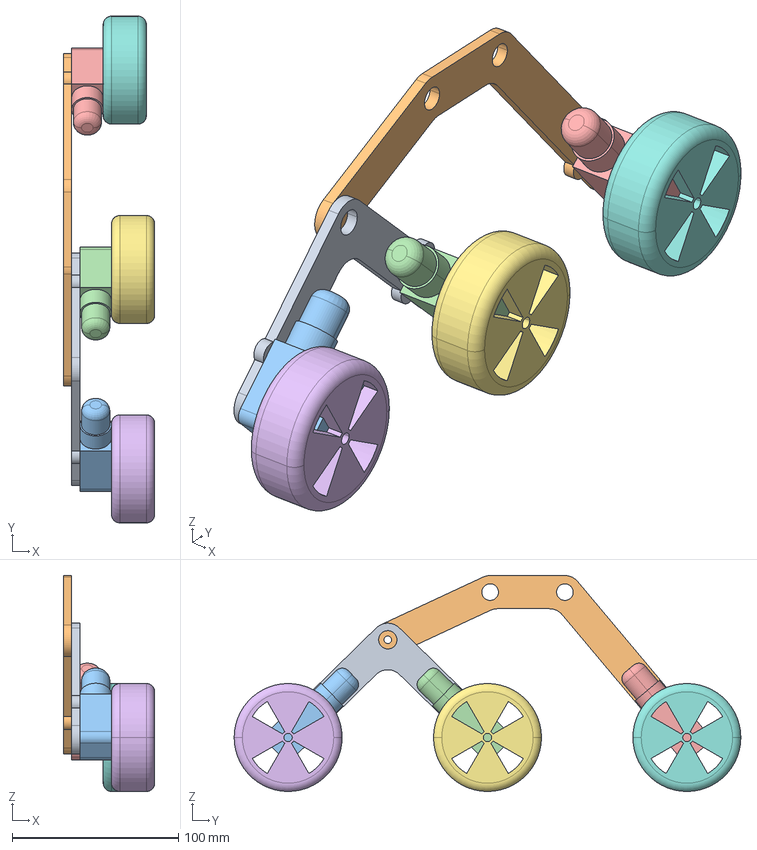
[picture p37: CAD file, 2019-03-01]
Hardware/FreeCad/rocker-bogie/rocker-bogie_assambley.fcstd
55.0 x 305.0 x 130.0 mm
Product1.1
Product1.002
Product1.003
Product1.004
Product1.005
Product1.006
Product1.007
Product1.008

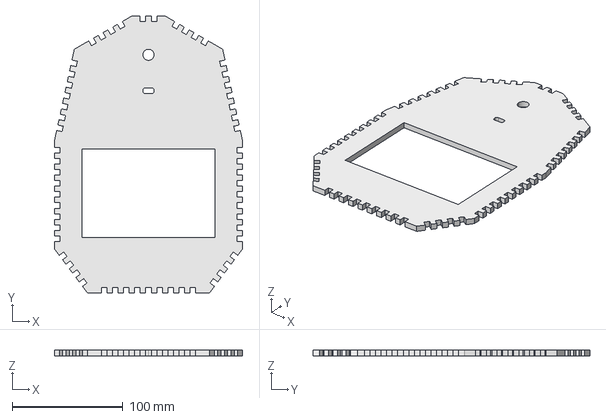
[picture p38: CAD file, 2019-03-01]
Hardware/FreeCad/chasis/top.fcstd
170.0 x 250.0 x 5.00 mm

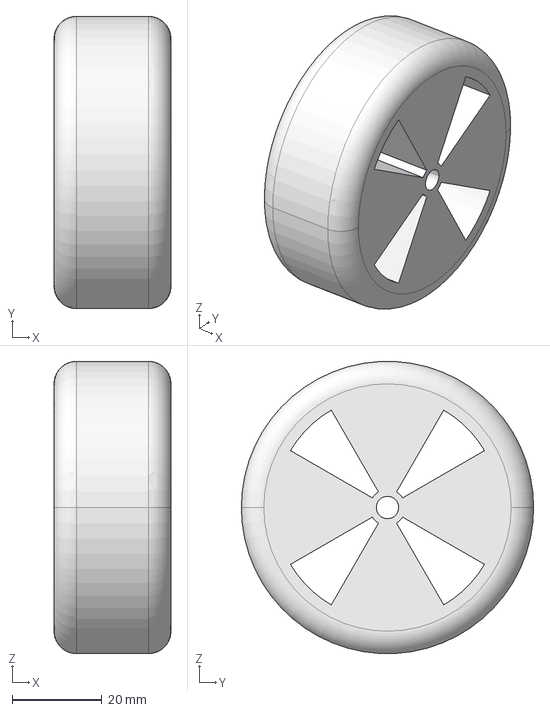
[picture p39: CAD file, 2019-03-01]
Hardware/FreeCad/rocker-bogie/wheel.fcstd
26.0 x 65.0 x 64.9 mm

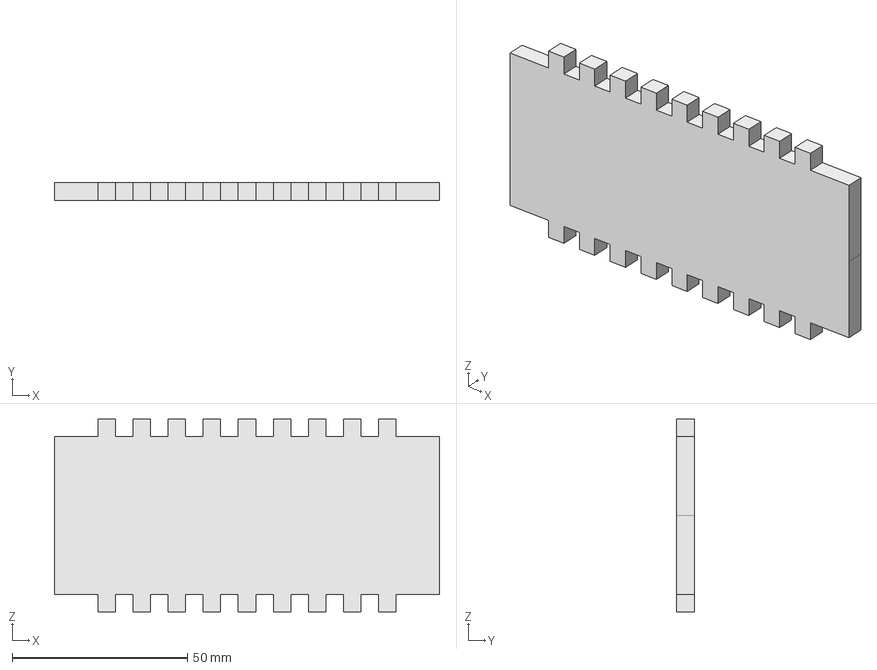
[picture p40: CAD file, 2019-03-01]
Hardware/FreeCad/chasis/back.fcstd
110.0 x 5.00 x 55.0 mm

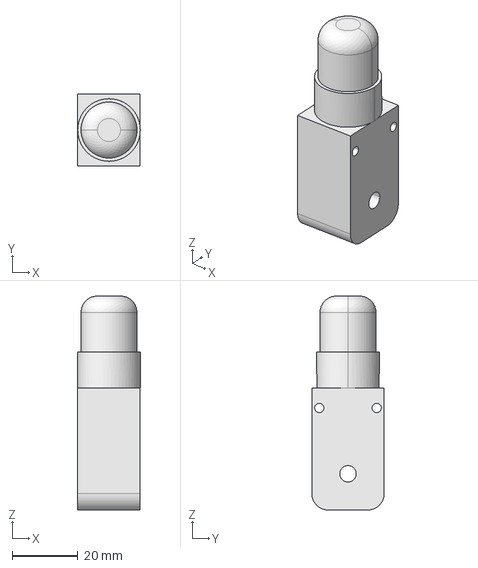
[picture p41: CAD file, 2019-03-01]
Hardware/FreeCad/rocker-bogie/dc_motor.fcstd
19.0 x 22.0 x 65.0 mm

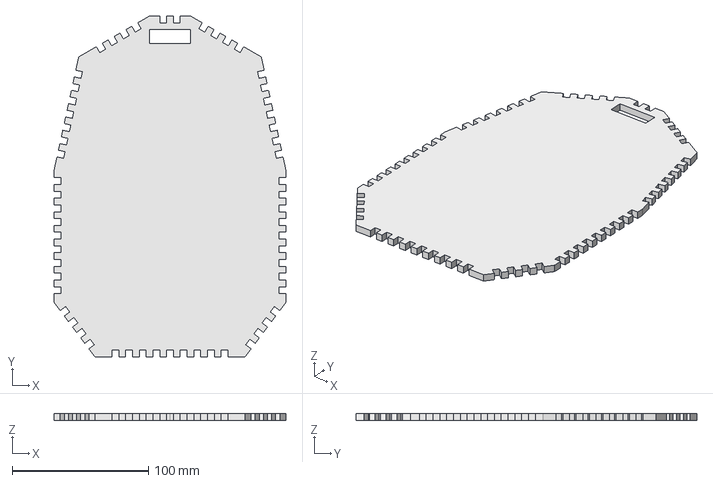
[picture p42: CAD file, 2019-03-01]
Hardware/FreeCad/chasis/bottom.fcstd
170.0 x 250.0 x 5.00 mm

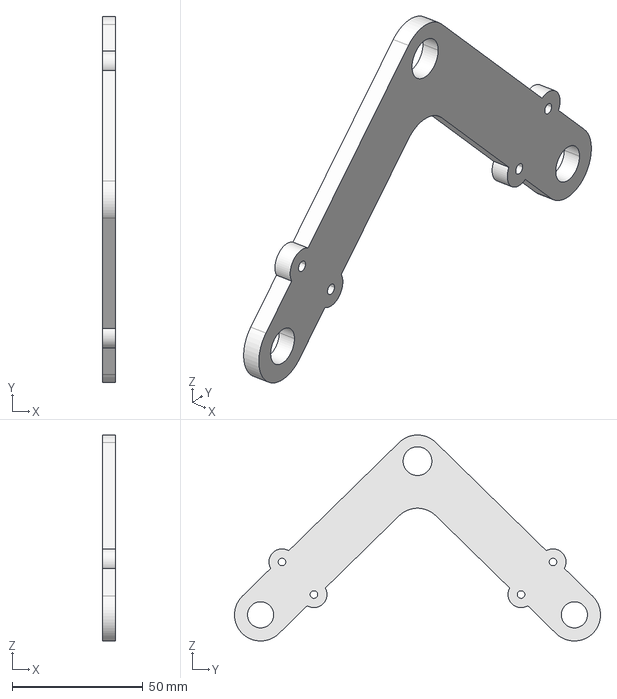
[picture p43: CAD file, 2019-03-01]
Hardware/FreeCad/rocker-bogie/rb_wheels.fcstd
5.00 x 140.0 x 78.8 mm

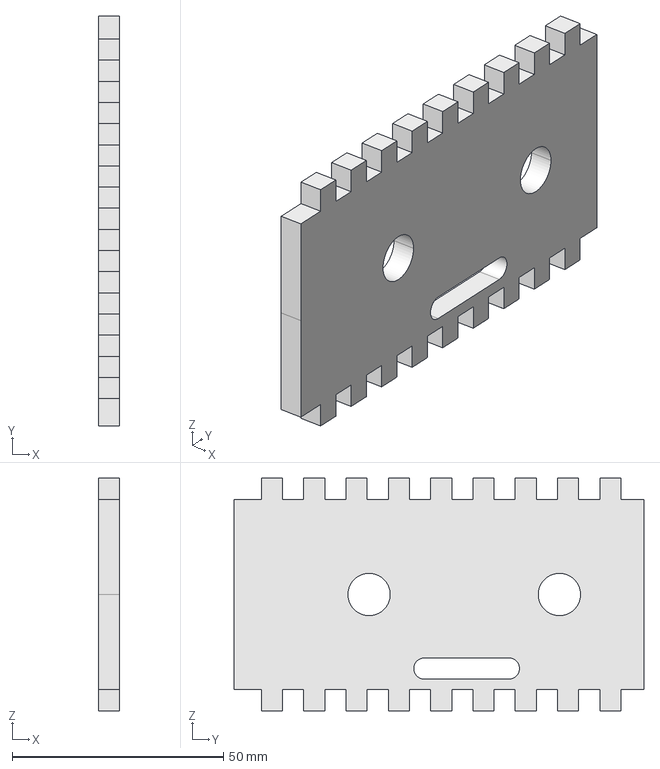
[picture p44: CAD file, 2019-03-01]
Hardware/FreeCad/chasis/union_ruedas.fcstd
5.00 x 96.9 x 55.0 mm

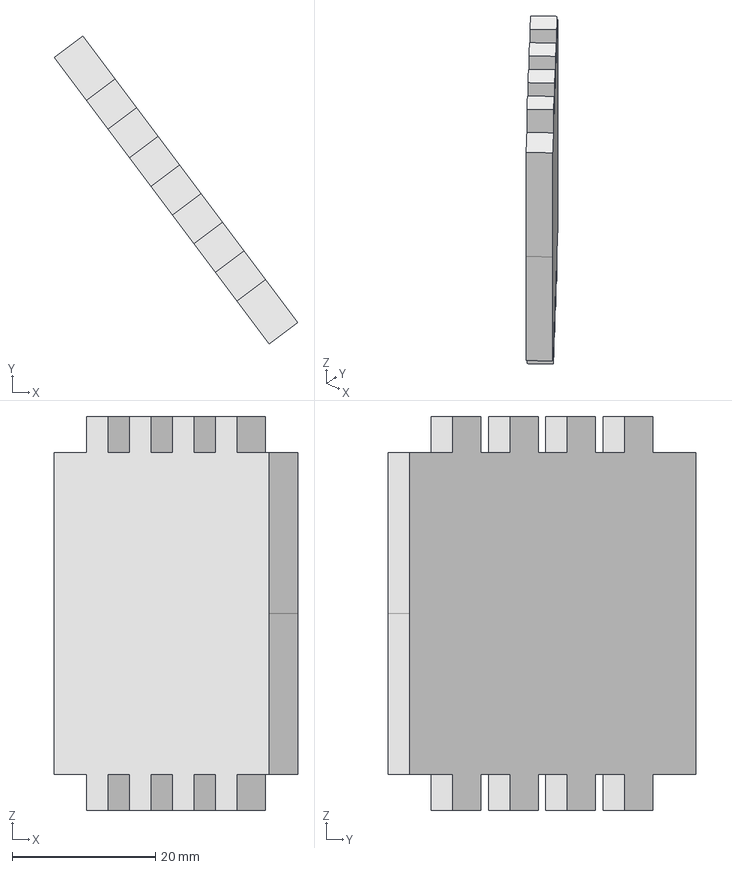
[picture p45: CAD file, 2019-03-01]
Hardware/FreeCad/chasis/back_sides.fcstd
34.0 x 43.0 x 55.0 mm

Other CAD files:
Hardware/encoders/optical_encoder_20160806-5704-fd9p8y-0.stl
Hardware/FreeCad/chasis/face_sides.fcstd

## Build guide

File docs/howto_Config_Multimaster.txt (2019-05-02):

#!/bin/bash

#http://www.iri.upc.edu/files/scidoc/1607-Multi-master-ROS-systems.pdf

# 1 bind names and ips moding /etc/hosts
# 2 multicast on
# 3 multicast adress using parameter (default 226.0.0.0)
# 4 ros local network routes

#### 1 #### 
sudo nano /etc/hosts
# Copias, pegas esto y descomentas las ips:
### Things for ros multimaster
## ip address	hostname
#192.168.1.39	chavalmi
#192.168.1.66	pi-desktop
#192.168.1.12	marrcogrova
###

#### 1.5 ####
gedit ~/.zshrc # or ~/.bashrc
# add this command at the end: export ROS_MASTER_URI=http://pi-desktop:11311
source ~/.zshrc

#### 2 ####
# check multicast is enable (next command return 0 if so)
cat /proc/sys/net/ipv4/icmp_echo_ignore_broadcasts
# temporary multicast (until restart): sudo sh -c "echo 0 >/proc/sys/net/ipv4/icmp_echo_ignore_broadcasts"
# permanently enable: mod this command or write it: net.ipv4.icmp_echo_ignore_broadcasts=0
sudo gedit /etc/sysctl.conf
sudo service procps restart # make changes to take effect
netstat -g # check which multicast groups are already defined in a computer
ping 224.0.0.1 # check multicast works, 224.0.0.1 is the standard ip, u will see it or not in previous cmd
# maybe u see (DUP!) tag, its ok 2 have duplicate pkgs

#### test ####
roscore
rosrun master_discovery_fkie master_discovery _mcast_group:=224.0.0.1 # in rpi
rosrun master_sync_fkie master_sync # in pc
rosservice call /master_discovery/list_masters # Check

#### 4 #### NO HAGAI NA DE ESTO

### DONT DO THIS ON THE GATEWAY!!
### to temporary set the default gateway:
#route add default gw <IP address>
## whereIP addressis the IP address of the device working as the gateway
## If multiple network interfaces are available, append dev <interface> to the previous command
#route add default gw <IP address> dev <interface>
## where interface is the one through which the current computer is connected to the gateway
### to permanently set the default gateway:
sudo nano /etc/network/if-up.d/multimaster_things
## copy this:
# #!/bin/bash
#
# if [ "$IFACE" = "<interface>" ]; then
# 	route add default gw <IP address>
# fi
chmod a+x /etc/network/if-up.d/multimaster_things

### Enable ip_forward on the gateway
# check ip_foward is enabled (next command return 1 if so)
cat /proc/sys/net/ipv4/icmp_echo_ignore_broadcasts
# temporary ip_foward (until restart): 
sudo sh -c "echo 1 >/proc/sys/net/ipv4/ip_forward"
# permanently enable: mod this command or write it: net.ipv4.ip_forward=1
#sudo nano /etc/sysctl.conf
#sudo service procps restart # make changes to take effect

###Add static routes between networks
#route add -net <local network> netmask 255.255.255.0 gw <common network gateway>
## or if it is a router work your own shit out

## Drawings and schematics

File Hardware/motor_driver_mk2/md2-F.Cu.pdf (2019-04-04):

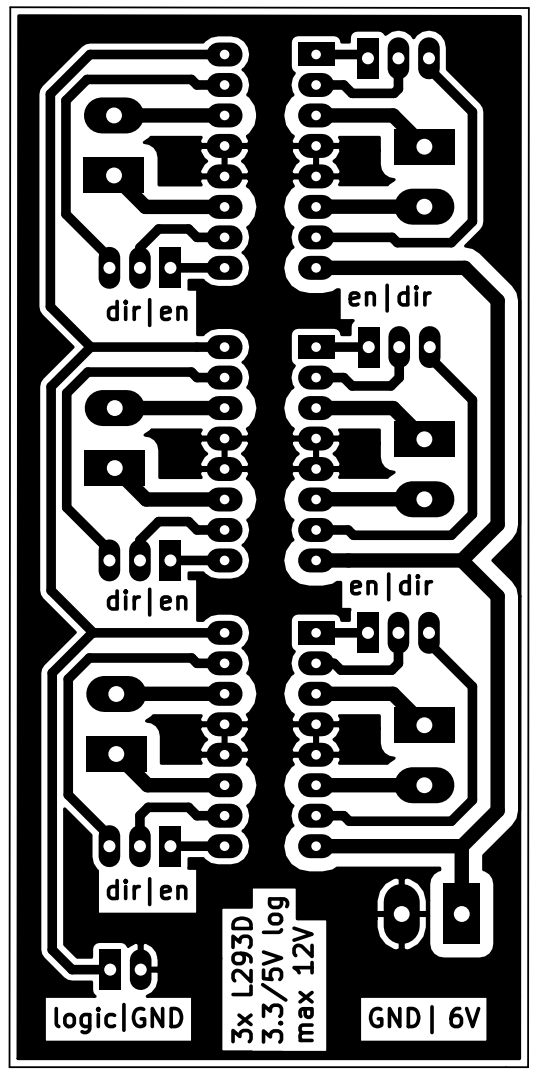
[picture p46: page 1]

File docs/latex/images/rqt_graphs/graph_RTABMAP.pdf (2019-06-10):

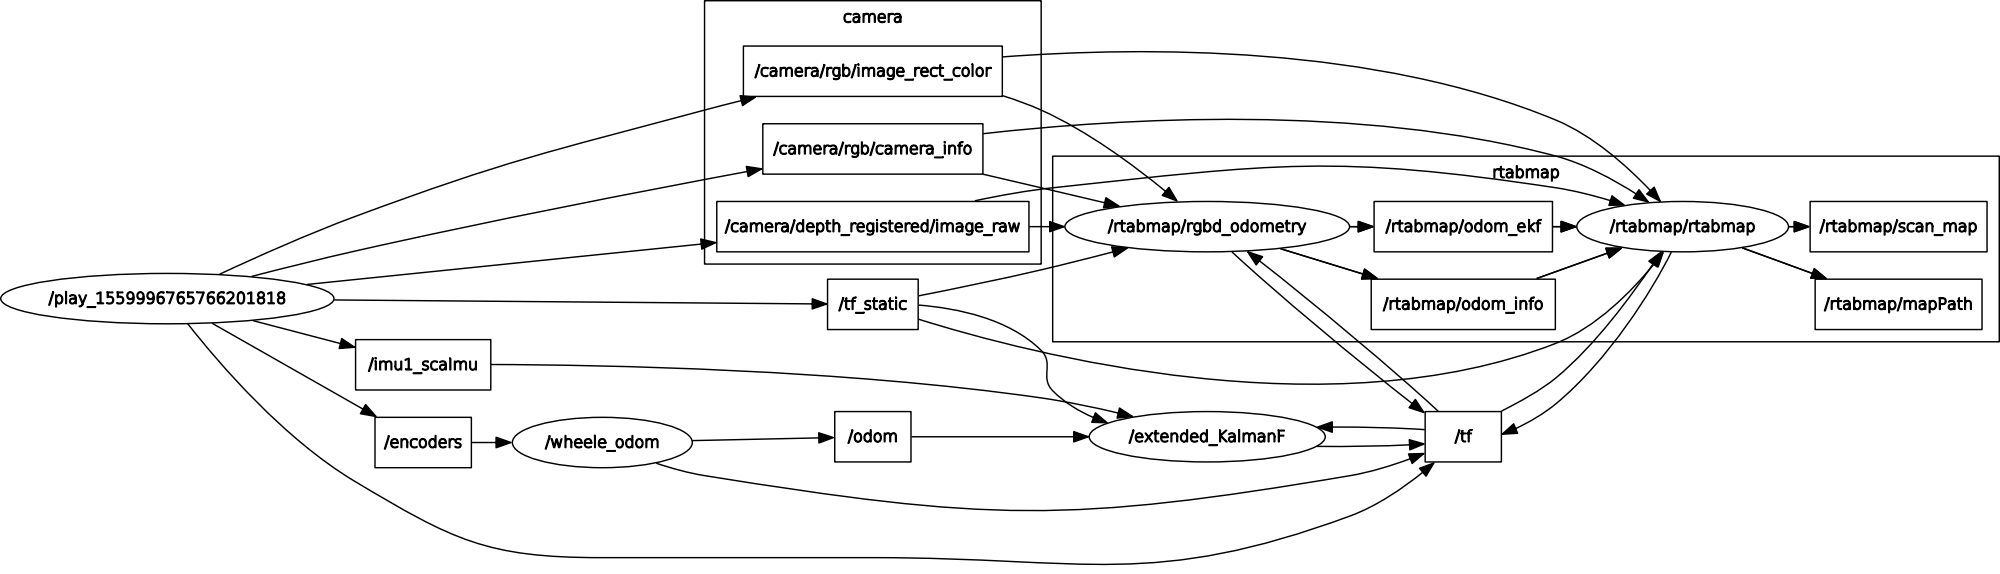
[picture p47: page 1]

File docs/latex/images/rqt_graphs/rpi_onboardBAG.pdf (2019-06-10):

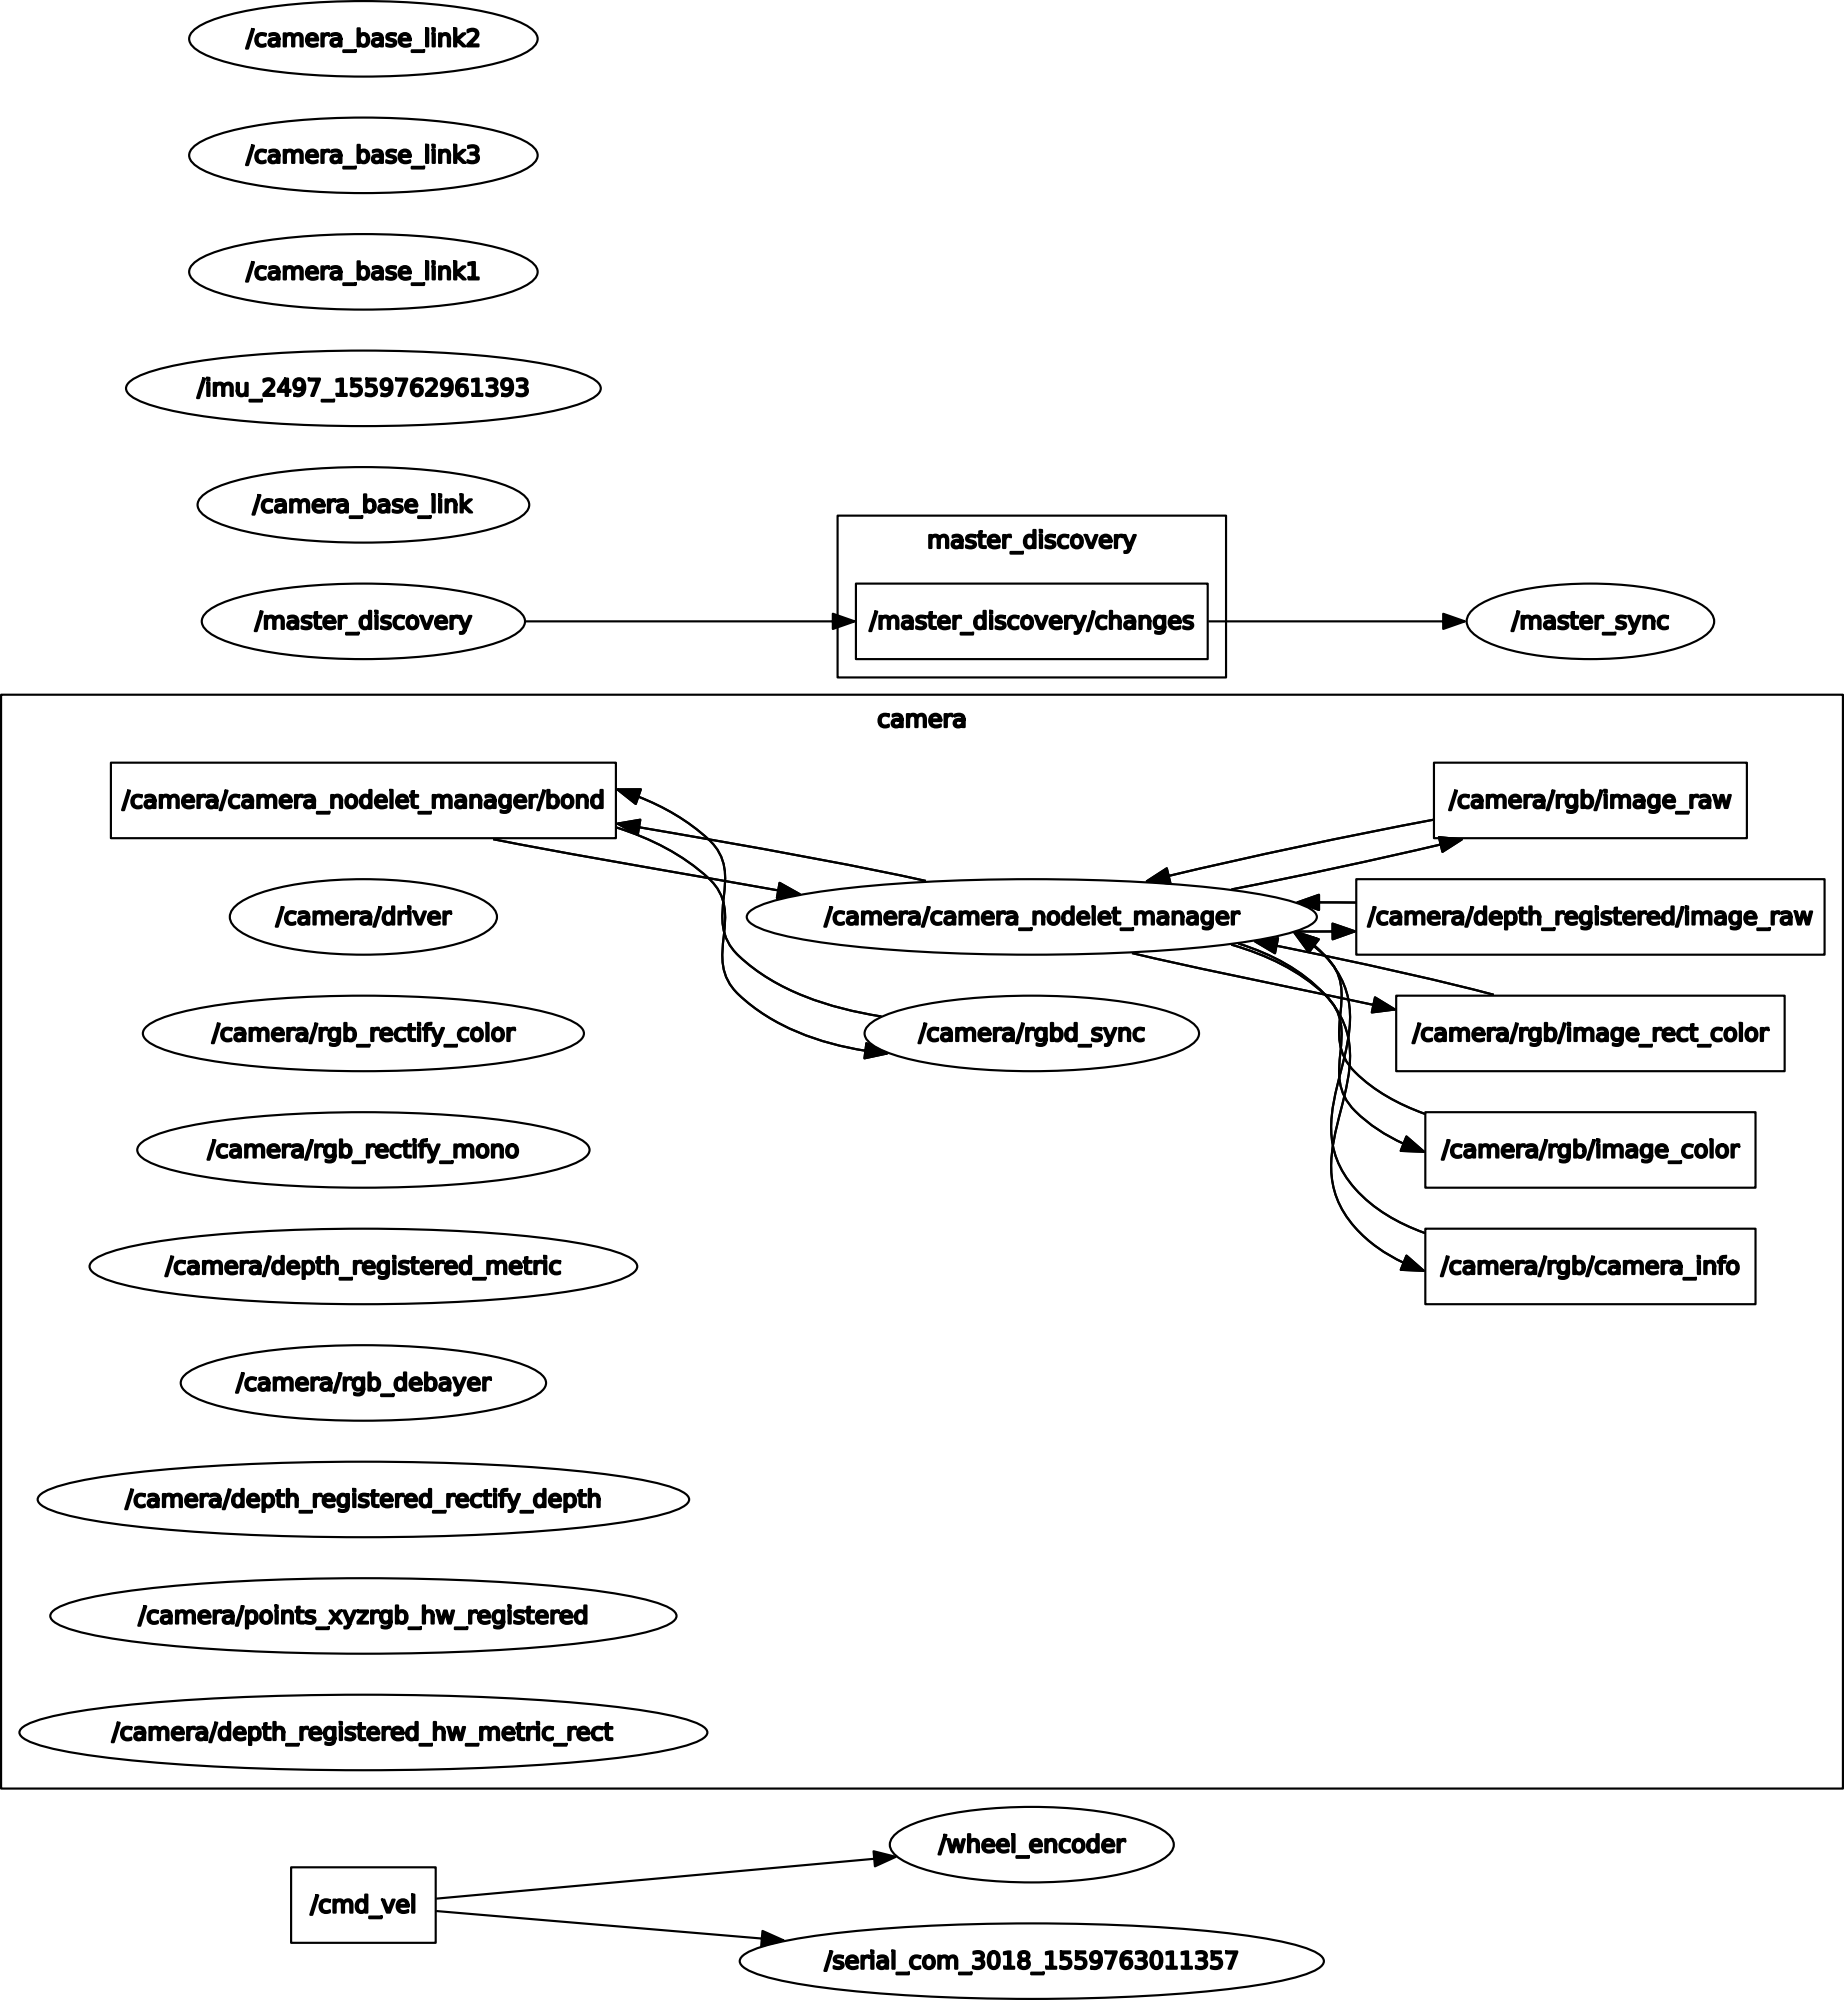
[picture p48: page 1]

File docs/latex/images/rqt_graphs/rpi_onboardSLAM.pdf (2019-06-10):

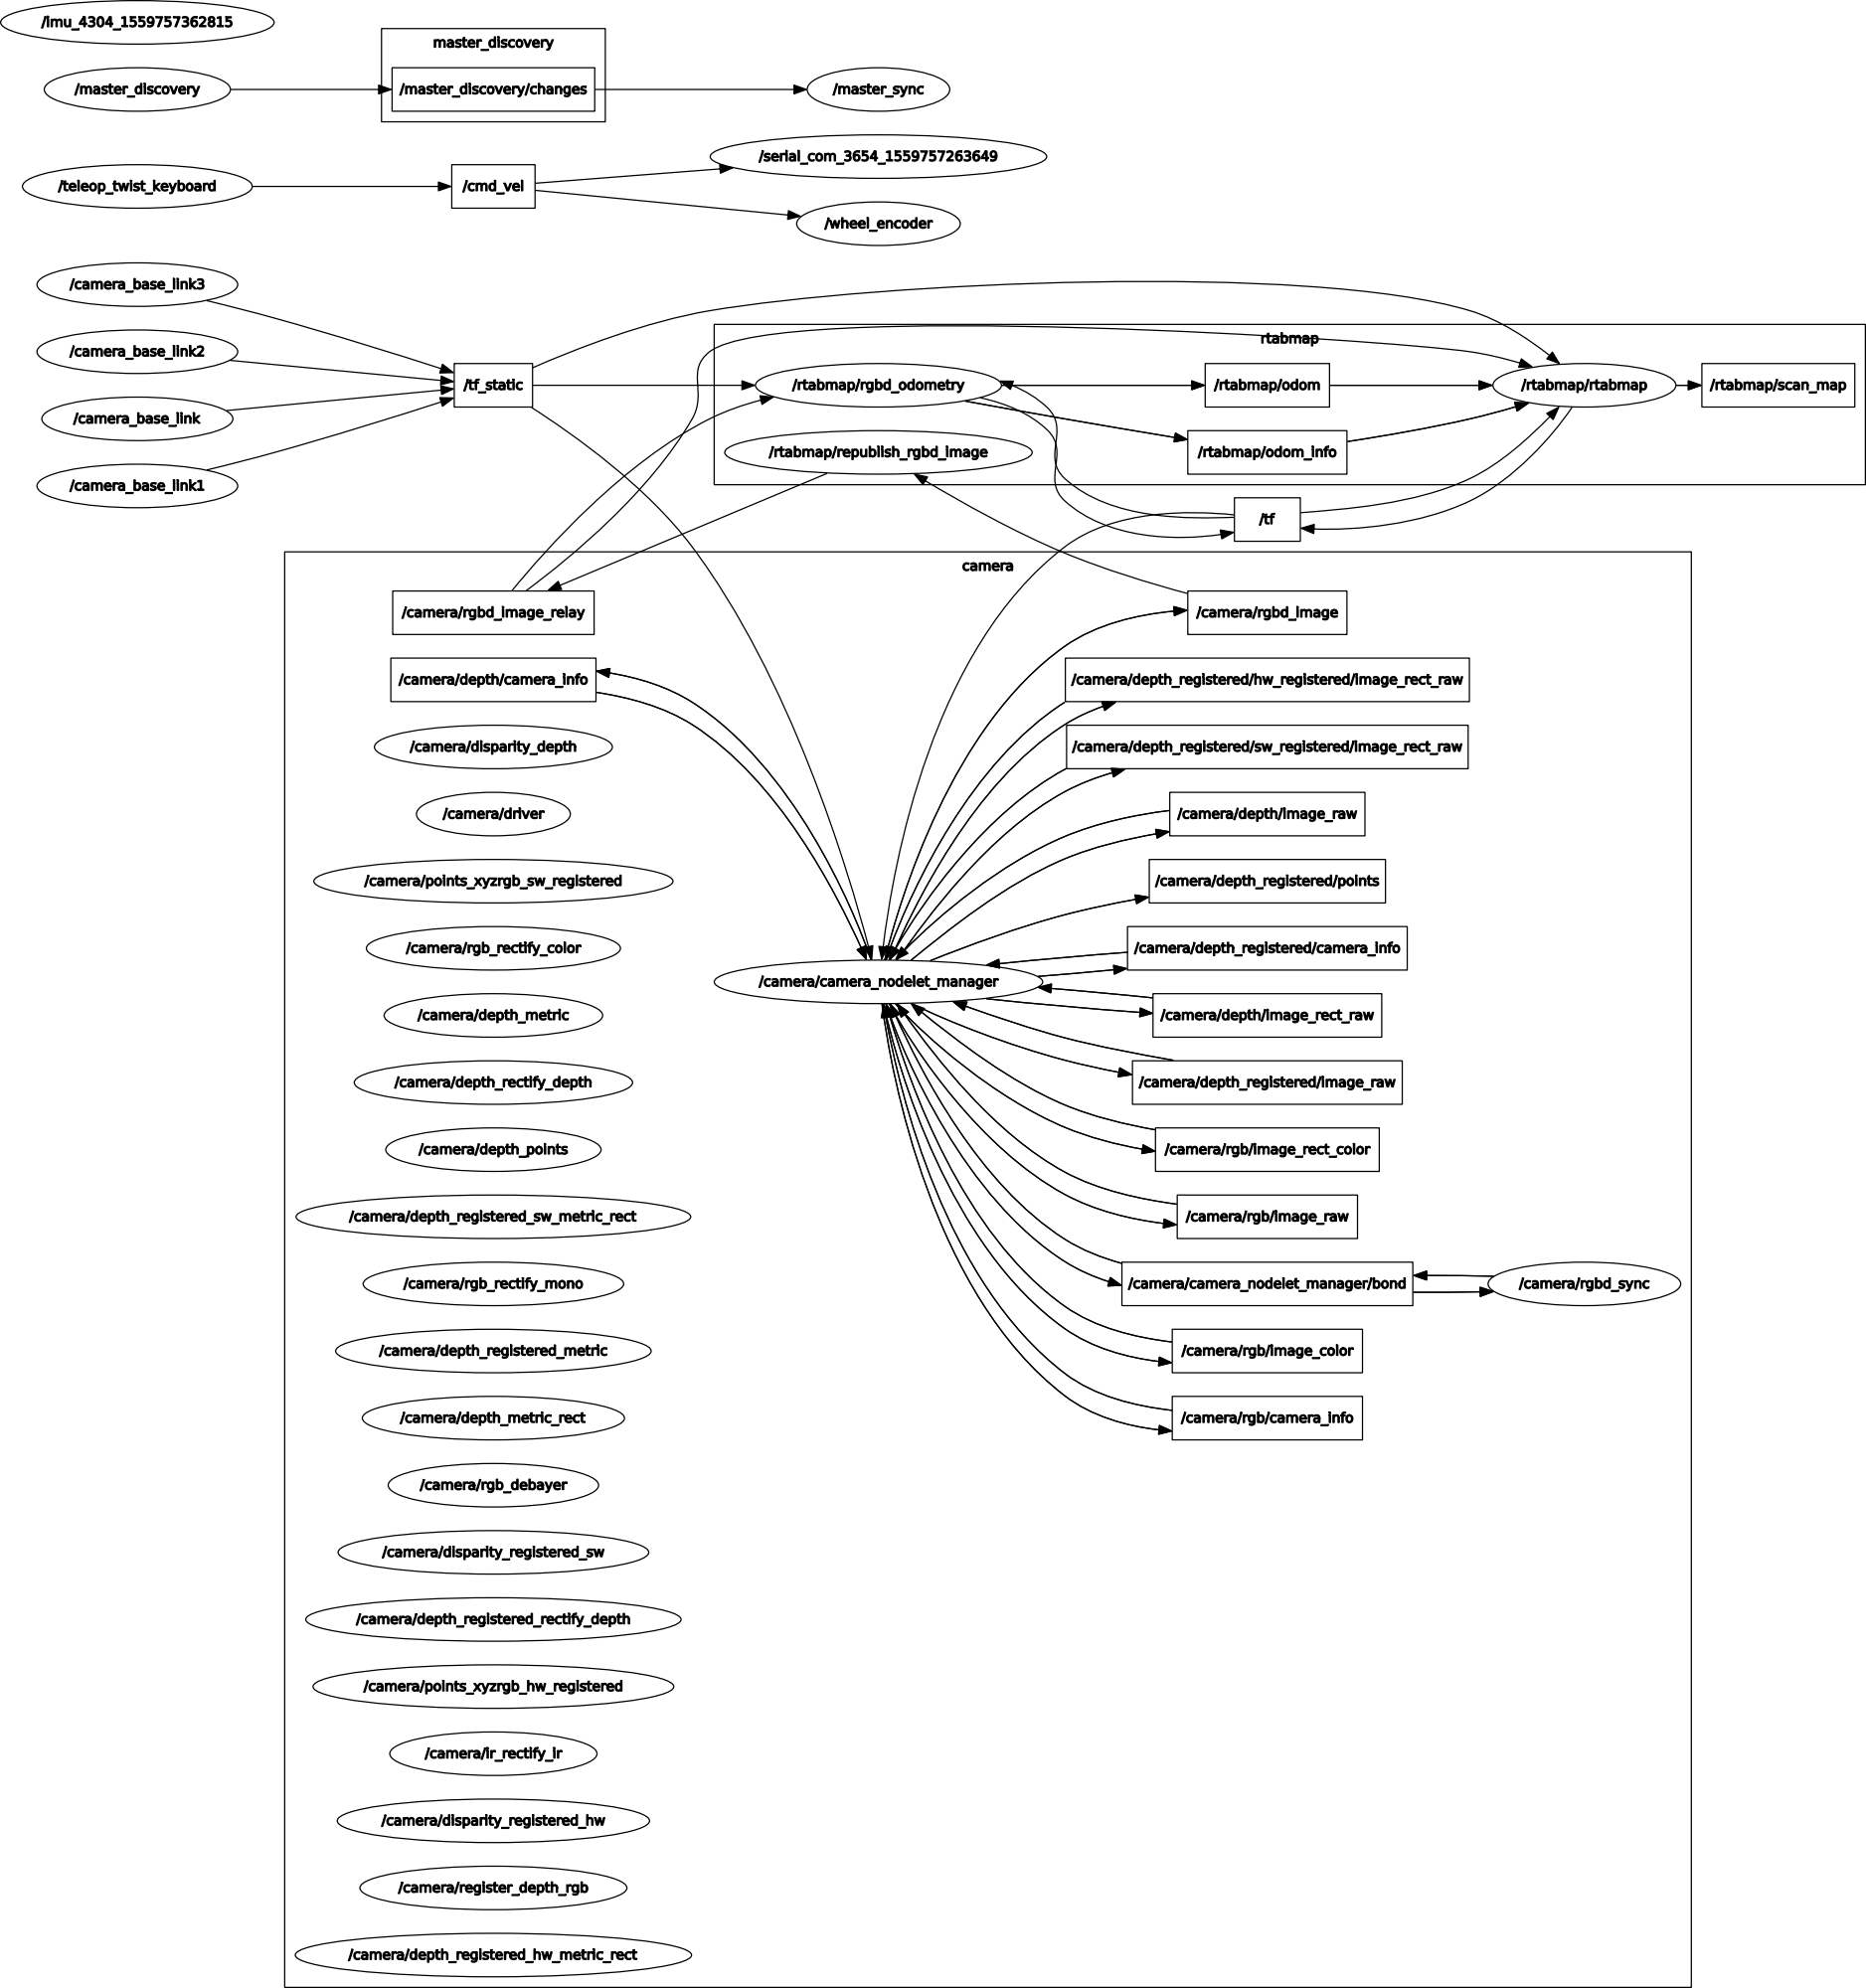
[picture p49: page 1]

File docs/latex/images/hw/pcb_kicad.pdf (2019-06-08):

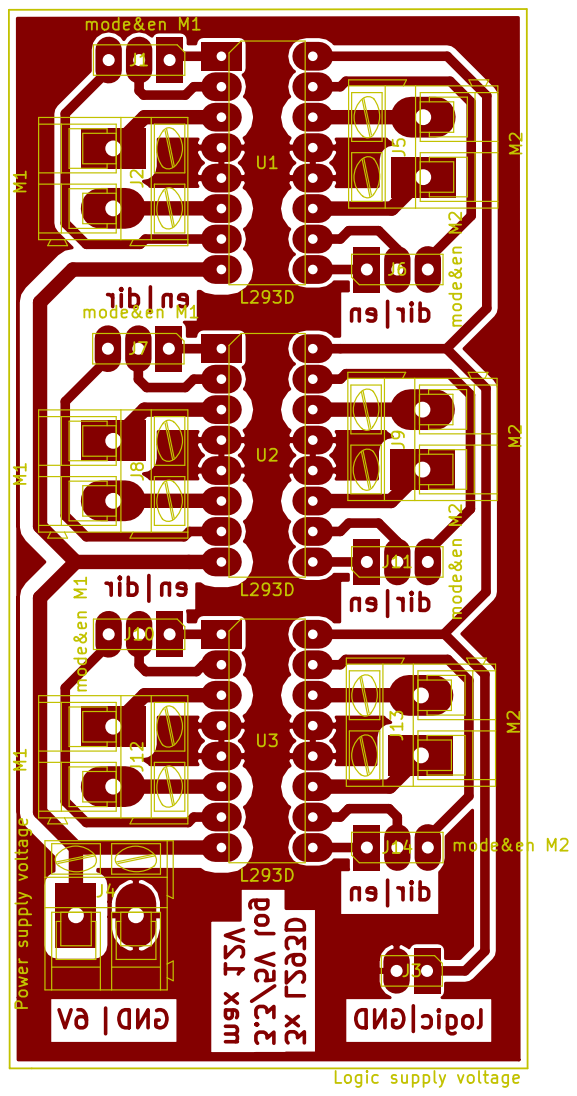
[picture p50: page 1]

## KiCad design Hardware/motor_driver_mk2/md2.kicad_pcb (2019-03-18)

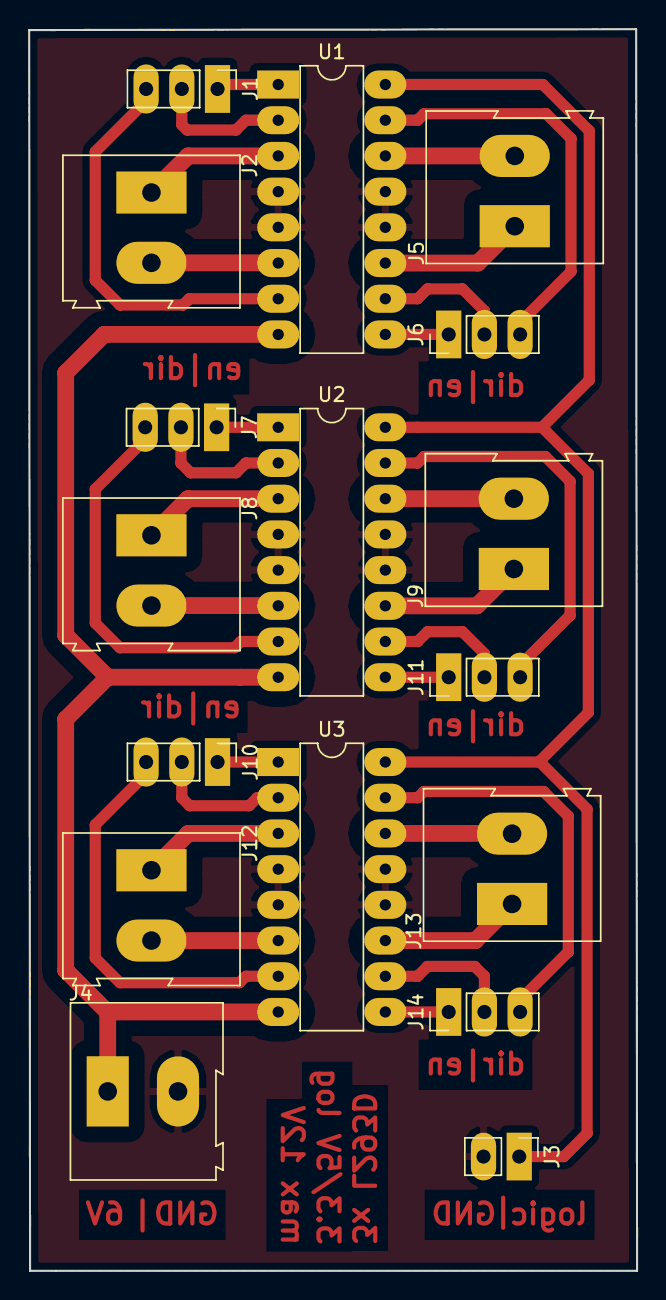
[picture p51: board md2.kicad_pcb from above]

Board: 2 copper layers, 43.2 x 88.3 mm, 17 parts (0 on the bottom side), 32 nets.

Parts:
J1, J7, J10: mode&en M1; Pin_Header_Straight_1x03_Pitch2.54mm
J2, J8, J12: M1; TerminalBlock_Altech_AK300-2_P5.00mm
J3: Logic supply voltage; Pin_Header_Straight_1x02_Pitch2.54mm
J4: Power supply voltage; TerminalBlock_Altech_AK300-2_P5.00mm
J5, J9, J13: M2; TerminalBlock_Altech_AK300-2_P5.00mm
J6, J11, J14: mode&en M2; Pin_Header_Straight_1x03_Pitch2.54mm
U1, U2, U3: L293D; DIP-16_W7.62mm_LongPads

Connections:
/en1: J1.1, U1.1
/en2: J6.1, J14.1, U1.9, U3.9
/en12: J7.1, U2.1
/en13: J10.1, U3.1
/en22: J11.1, U2.9
/m1+: J2.1, U1.3
/m1+2: J8.1, U2.3
/m1+3: J12.1, U3.3
/m1-: J2.2, U1.6
/m1-2: J8.2, U2.6
/m1-3: J12.2, U3.6
/m2+: J5.1, U1.11
/m2+2: J9.1, U2.11
/m2+3: J13.1, U3.11
/m2-: J5.2, U1.14
/m2-2: J9.2, U2.14
/m2-3: J13.2, U3.14
/mode1+: J1.2, U1.2
/mode1+2: J7.2, U2.2
/mode1+3: J10.2, U3.2
/mode1-: J1.3, U1.7
/mode1-2: J7.3, U2.7
/mode1-3: J10.3, U3.7
/mode2+: J6.2, U1.10
/mode2+2: J11.2, U2.10
/mode2+3: J14.2, U3.10
/mode2-: J6.3, U1.15
/mode2-2: J11.3, U2.15
/mode2-3: J14.3, U3.15
GND: J3.2, J4.2, U1.4, U1.5, U1.12, U1.13, U2.4, U2.5, U2.12, U2.13, U3.4, U3.5, U3.12, U3.13
ardu5v: J3.1, U1.16, U2.16, U3.16
supply: J4.1, U1.8, U2.8, U3.8

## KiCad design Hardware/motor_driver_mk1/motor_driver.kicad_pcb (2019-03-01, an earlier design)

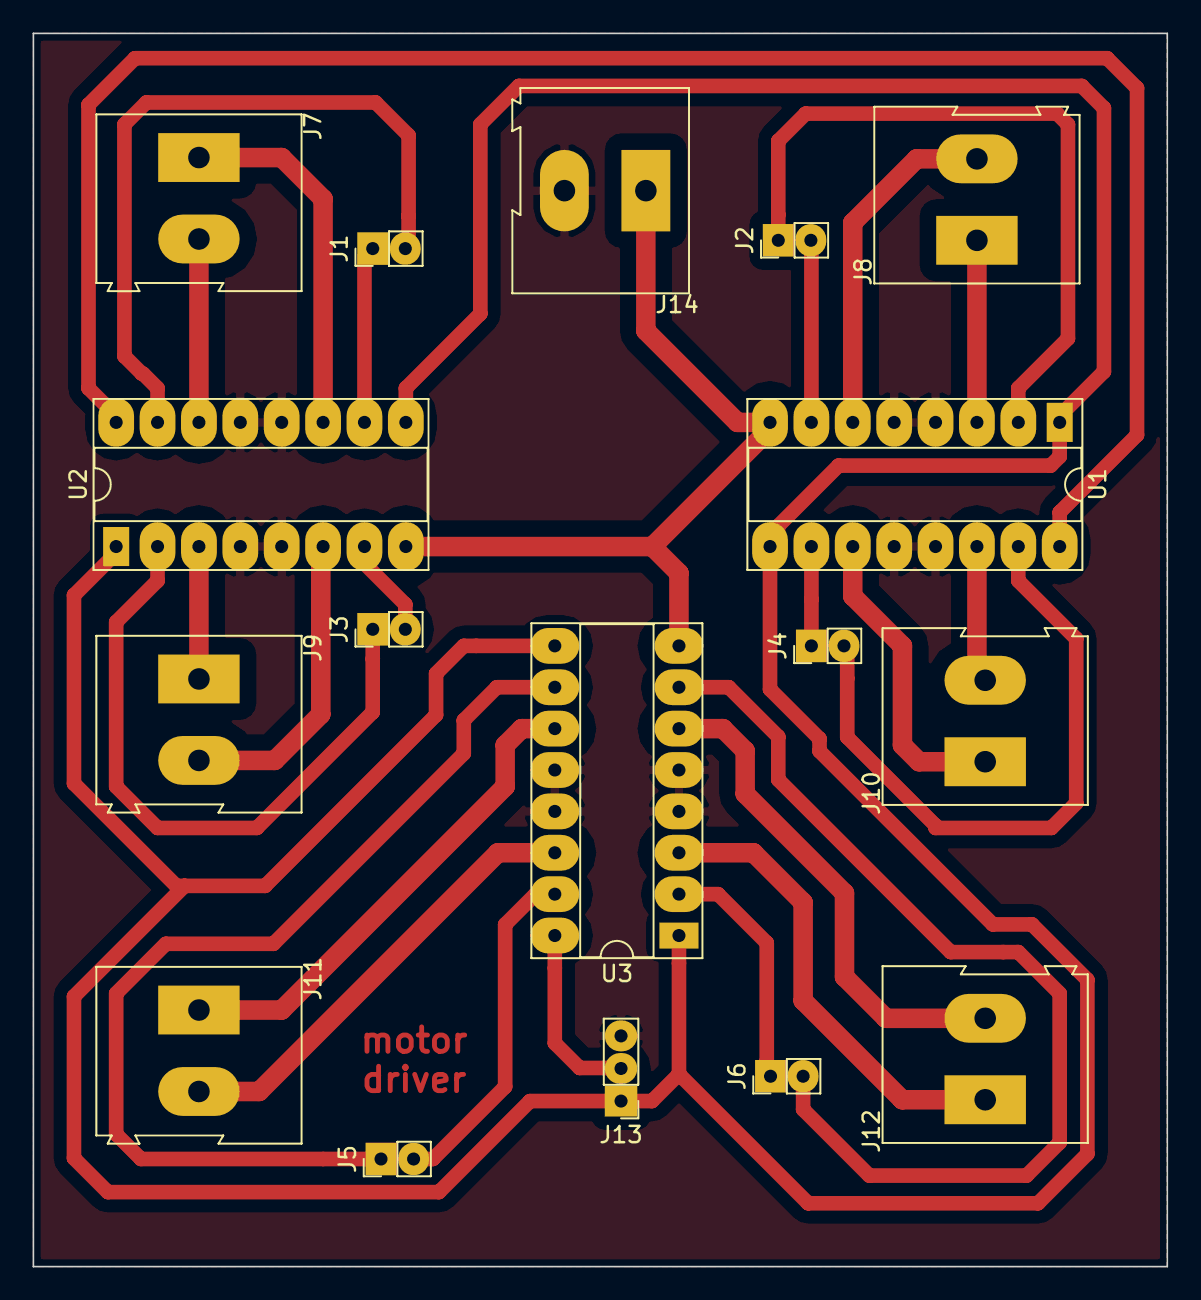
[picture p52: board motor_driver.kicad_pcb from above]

Board: 2 copper layers, 69.6 x 75.7 mm, 17 parts (0 on the bottom side), 28 nets.

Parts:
J1, J2, J3, J4, J5, J6: Conn_01x02; Pin_Header_Straight_1x02_Pitch2.00mm
J7: m1; TerminalBlock_Altech_AK300-2_P5.00mm
J8: m2; TerminalBlock_Altech_AK300-2_P5.00mm
J9: m3; TerminalBlock_Altech_AK300-2_P5.00mm
J10: m4; TerminalBlock_Altech_AK300-2_P5.00mm
J11: m5; TerminalBlock_Altech_AK300-2_P5.00mm
J12: m6; TerminalBlock_Altech_AK300-2_P5.00mm
J13: Conn_01x03; Pin_Header_Straight_1x03_Pitch2.00mm
J14: power12v; TerminalBlock_Altech_AK300-2_P5.00mm
U1, U2, U3: L293D; DIP-16_W7.62mm_Socket_LongPads

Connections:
GND: J13.3, J14.2, U1.4, U1.5, U1.12, U1.13, U2.4, U2.5, U2.12, U2.13, U3.4, U3.5, U3.12, U3.13
ardu5V: J13.2, U1.16, U2.16, U3.16
dig_m1: J1.2, U2.15
dig_m2: J2.2, U1.7
dig_m3: J3.2, U2.7
dig_m4: J4.2, U1.15
dig_m5: J5.2, U3.15
dig_m6: J6.2, U3.7
en: J13.1, U1.1, U1.9, U2.1, U2.9, U3.1, U3.9
m1+: J7.1, U2.11
m1-: J7.2, U2.14
m2+: J8.1, U1.3
m2-: J8.2, U1.6
m3+: J9.1, U2.3
m3-: J9.2, U2.6
m4+: J10.1, U1.11
m4-: J10.2, U1.14
m5+: J11.1, U3.11
m5-: J11.2, U3.14
m6+: J12.1, U3.3
m6-: J12.2, U3.6
pwm_m1: J1.1, U2.10
pwm_m2: J2.1, U1.2
pwm_m3: J3.1, U2.2
pwm_m4: J4.1, U1.10
pwm_m5: J5.1, U3.10
pwm_m6: J6.1, U3.2
supply12V: J14.1, U1.8, U2.8, U3.8

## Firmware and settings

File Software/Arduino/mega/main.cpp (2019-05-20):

#include <Arduino.h>
#include <string.h>
#include <CmdMessenger.h>
#define pi 3.141592
#define pix2 6.283184  //2pi
#define t_cntl 0.016383 //seconds = 16.383ms = 61Hz

/*
ENABLE(PWM) |      A       |     B        |   STATUS           |
--------------------------------------------------------- |
     LOW    |    ----      |    ----      |MOTOR PARADO        |
     HIGH   |    HIGH      |     LOW      |MOTOR GIRA DELANTE  |
     HIGH   |    LOW       |     HIGH     |MOTOR GIRA AL REVES |
     HIGH   |    HIGH      |     HIGH     |MOTOR PARADO        |
     HIGH   |    LOW       |     LOW      |MOTOR PARADO        |
 */

/* Define the Motors pin numbers */
#define m1L_en 4
#define m2L_en 5
#define m3L_en 6
#define m1R_en 7
#define m2R_en 8
#define m3R_en 9
// Motors directions
#define mL_a 0
#define mL_b 1
#define mR_a 14
#define mR_b 15

// Define the encoders pin numbers
#define m1l_encoder 2 //INTF4
#define m2l_encoder 3 //INTF5
#define m3l_encoder 18  //INTF3
#define m1r_encoder 19  //INTF2
#define m2r_encoder 20  //INTF1
#define m3r_encoder 21  //INTF0
// Encoders data
#define slits_arc 7.5 // Grades between slits
#define number_slits 22

//Debug purpose leds
#define led1 23
#define led2 22

/* INTERRUPTS & TIMERS
Timer 2: 8bit timer with overflow interrupt for account time
Timer 1: 16bit timer that provides synchronous control (prescle & max configured in setup)
m1l_isr(): Rising edge interrupt that save time to compute rad/s
*/
volatile boolean m1l_first,m1l_triggered,m2l_first,m2l_triggered,m3l_first,m3l_triggered;
volatile boolean m1r_first,m1r_triggered,m2r_first,m2r_triggered,m3r_first,m3r_triggered;
volatile unsigned long m1l_startTime, m1l_finishTime,m2l_startTime, m2l_finishTime,m3l_startTime, m3l_finishTime;
volatile unsigned long m1r_startTime, m1r_finishTime,m2r_startTime, m2r_finishTime,m3r_startTime, m3r_finishTime;
volatile unsigned long overflowCount;
volatile bool flag_cntl;
volatile bool flag_serial;

ISR (TIMER2_OVF_vect) { // timer overflows (every 65536 counts)
  overflowCount++;
}  // end of TIMER1_OVF_vect

ISR( TIMER1_COMPA_vect){
  flag_cntl = true;
  flag_serial=true;
  TIMSK1=0;
}

void m1l_isr () {
  unsigned int counter = TCNT2;  // quickly save it
  // wait until we noticed last one
  if (m1l_triggered)
    return;
  if (m1l_first){
    m1l_startTime = (overflowCount << 8) + counter;
    m1l_first= false;
    return;
  }
  m1l_finishTime = (overflowCount << 8) + counter;
  m1l_triggered = true;
  detachInterrupt(digitalPinToInterrupt(m1l_encoder));
}  // end of isr
void m2l_isr () {
  unsigned int counter = TCNT2;  // quickly save it
  // wait until we noticed last one
  if (m2l_triggered)
    return;
  if (m2l_first){
    m2l_startTime = (overflowCount << 8) + counter;
    m2l_first= false;
    return;
  }
  m2l_finishTime = (overflowCount << 8) + counter;
  m2l_triggered = true;
  detachInterrupt(digitalPinToInterrupt(m2l_encoder));
}  // end of isr
void m3l_isr () {
  unsigned int counter = TCNT2;  // quickly save it
  // wait until we noticed last one
  if (m3l_triggered)
    return;
  if (m3l_first){
    m3l_startTime = (overflowCount << 8) + counter;
    m3l_first= false;
    return;
  }
  m3l_finishTime = (overflowCount << 8) + counter;
  m3l_triggered = true;
  detachInterrupt(digitalPinToInterrupt(m3l_encoder));
}  // end of isr
void m1r_isr () {
  unsigned int counter = TCNT2;  // quickly save it
  // wait until we noticed last one
  if (m1r_triggered)
    return;
  if (m1r_first){
    m1r_startTime = (overflowCount << 8) + counter;
    m1r_first= false;
    return;
  }
  m1r_finishTime = (overflowCount << 8) + counter;
  m1r_triggered = true;
  detachInterrupt(digitalPinToInterrupt(m1r_encoder));
}  // end of isr
void m2r_isr () {
  unsigned int counter = TCNT2;  // quickly save it
  // wait until we noticed last one
  if (m2r_triggered)
    return;
  if (m2r_first){
    m2r_startTime = (overflowCount << 8) + counter;
    m2r_first= false;
    return;
  }
  m2r_finishTime = (overflowCount << 8) + counter;
  m2r_triggered = true;
  detachInterrupt(digitalPinToInterrupt(m2r_encoder));
}  // end of isr
void m3r_isr () {
  unsigned int counter = TCNT2;  // quickly save it
  // wait until we noticed last one
  if (m3r_triggered)
    return;
  if (m3r_first){
    m3r_startTime = (overflowCount << 8) + counter;
    m3r_first= false;
    return;
  }
  m3r_finishTime = (overflowCount << 8) + counter;
  m3r_triggered = true;
  detachInterrupt(digitalPinToInterrupt(m3r_encoder));
}  // end of isr

void setup_m1l_isr(){ // get ready for next time
  EIFR = bit (INTF4);  // clear flag for interrupt 0
  m1l_first = true;
  m1l_triggered = false;  // re-arm for next time
  attachInterrupt(digitalPinToInterrupt(m1l_encoder), m1l_isr, RISING);
}  // end of prepareForInterrupts
void setup_m2l_isr(){ // get ready for next time
  EIFR = bit (INTF5);  // clear flag for interrupt 0
  m2l_first = true;
  m2l_triggered = false;  // re-arm for next time
  attachInterrupt(digitalPinToInterrupt(m2l_encoder), m2l_isr, RISING);
}
void setup_m3l_isr(){ // get ready for next time
  EIFR = bit (INTF3);  // clear flag for interrupt 0
  m3l_first = true;
  m3l_triggered = false;  // re-arm for next time
  attachInterrupt(digitalPinToInterrupt(m3l_encoder), m3l_isr, RISING);
}
void setup_m1r_isr(){ // get ready for next time
  EIFR = bit (INTF2);  // clear flag for interrupt 0
  m1r_first = true;
  m1r_triggered = false;  // re-arm for next time
  attachInterrupt(digitalPinToInterrupt(m1r_encoder), m1r_isr, RISING);
}
void setup_m2r_isr(){ // get ready for next time
  EIFR = bit (INTF1);  // clear flag for interrupt 0
  m2r_first = true;
  m2r_triggered = false;  // re-arm for next time
  attachInterrupt(digitalPinToInterrupt(m2r_encoder), m2r_isr, RISING);
}
void setup_m3r_isr(){ // get ready for next time
  EIFR = bit (INTF0);  // clear flag for interrupt 0
  m3r_first = true;
  m3r_triggered = false;  // re-arm for next time
  attachInterrupt(digitalPinToInterrupt(m3r_encoder), m3r_isr, RISING);
}
void setup_isr(){
  setup_m1l_isr();
  setup_m2l_isr();
  setup_m3l_isr();
  setup_m1r_isr();
  setup_m2r_isr();
  setup_m3r_isr();
}

/* ACTION & CONTROL STUFF
-No hay Kp y Ki para cada motor es cuestion de añadir otro switch como en control.cpp
+Antiwindup 4
+ It should be runned without interrupts (as serial stuff)
*/

void write_pwm(int enable,int pwm, int dir1, int dir2){ //function to write pwm 2 motors & manage directions

    if(pwm > 0){
      if (pwm>255) pwm=255;
        digitalWrite(dir1, HIGH);
        digitalWrite(dir2, LOW);
        analogWrite(enable, pwm);
    }
    else if(pwm < 0){
      if (pwm<-255) pwm=-255;
        digitalWrite(dir1, LOW);
        digitalWrite(dir2, HIGH);
        analogWrite(enable, abs(pwm));
    }
    else{
        digitalWrite(enable, LOW);
    }
}

unsigned long kp=13.0,ki=0.9;
static float sat_err_m1l,i_m1l,sat_err_m2l,i_m2l,sat_err_m3l,i_m3l;
static float sat_err_m1r,i_m1r,sat_err_m2r,i_m2r,sat_err_m3r,i_m3r;

float control_law(int m, float ref, float out, float i,float sat_err, float sample_time){
  float sat_err_integrated, ek, ukns, ukreal, p;
  sat_err_integrated=(float)sat_err*sample_time;  // Integration of how much we satured
  ek = (float)ref-(float)out;  // Error = Desired - Actual(output)
  p = kp*ek;
  i = ki*(i+ek*sample_time);
  //d = kd*((ek-ek1)*61.0);
  ukns=p+i+(sat_err_integrated/0.1);//+d
  if(ukns<-255) ukreal=-255.0;  // Saturation
  else if(ukns>255) ukreal=255.0;
  else ukreal=ukns;
  sat_err=ukreal-ukns;  // Saturation error
  //ek1=ek; // Error update
  switch(m){  // Store saturation error, integral term & (just if derivative effect is used) error
    case 1:
      sat_err_m1l=sat_err;
      i_m1l=i;
      //ek1_m1l=ek1;
      break;
    case 2:
      sat_err_m1r=sat_err;
      i_m1r=i;
      //ek1_m1l=ek1;
      break;
    case 3:
      sat_err_m2l=sat_err;
      i_m2l=i;
      //ek1_m2l=ek1;
      break;
    case 4:
      sat_err_m2r=sat_err;
      i_m2r=i;
      //ek1_m2r=ek1;
      break;
    case 5:
      sat_err_m3l=sat_err;
      i_m3l=i;
      //ek1_m3l=ek1;
      break;
    case 6:
      sat_err_m3r=sat_err;
      i_m3r=i;
      //ek1_m3r=ek1;
      break;
  }
  return ukreal;
}


void shutdown_motors() { // Apagar los motores
  write_pwm(m1L_en,0, mL_a,mL_b);
  write_pwm(m2L_en,0, mL_a,mL_b);
  write_pwm(m3L_en,0, mL_a,mL_b);

  write_pwm(m1R_en,0, mR_a,mR_b);
  write_pwm(m2R_en,0, mR_a,mR_b);
  write_pwm(m3R_en,0, mR_a,mR_b);
}

/*  SERIAL STUFF
https://github.com/thijse/Arduino-CmdMessenger
https://github.com/zivlab/PyCmdMessenger
+ It should be used without interrupts on, bc it uses some of thems (idk which ones)
+ Tenemos todos los comandos que ves en enum
      cmd_off: para todo
      receive_ref: take reference in rad/s from pc
      send_encoder: send all 6 encoders data in rad/s to pc
      send_control_sig: send 6 pwm written to motors to pc
      change_kp: take kp from pc
      change_ki:
      request_ticks: if this cmd is received, send encoders data
      request_control_signal:
+ Example in cmd_serial_example
*/
bool controlling = 1; // 1 if control active & motors can run
CmdMessenger cmdMessenger = CmdMessenger(Serial); // Attach a new CmdMessenger object to the default Serial port
enum {
  cmd_off,  // Cmd to deactivate control & motors. Reset needed after this
  receive_ref,
  send_encoder,
  send_control_sig,
  change_kp,
  change_ki,
  request_ticks,
  request_control_signal,
};
void turn_off() {
  controlling = ! controlling; // Turn off control and motors
}
float left_ref, right_ref;
void take_ref(){
  left_ref = cmdMessenger.readBinArg<float>();
  right_ref = cmdMessenger.readBinArg<float>();
  //we could act here (?)
}
void on_change_kp(){
  kp = cmdMessenger.readBinArg<float>();
}
void on_change_ki(){
  ki = cmdMessenger.readBinArg<float>();
}
float m1l_rads=0,m2l_rads=0,m3l_rads=0,m1r_rads=0,m2r_rads=0,m3r_rads=0;
float m1l_pwm=0,m2l_pwm=0,m3l_pwm=0,m1r_pwm=0,m2r_pwm=0,m3r_pwm=0;
void on_request_ticks(){
  cmdMessenger.sendCmdStart(send_encoder);
  cmdMessenger.sendCmdBinArg(m1l_rads); cmdMessenger.sendCmdBinArg(m2l_rads); cmdMessenger.sendCmdBinArg(m3l_rads);
  cmdMessenger.sendCmdBinArg(m1r_rads); cmdMessenger.sendCmdBinArg(m2r_rads); cmdMessenger.sendCmdBinArg(m3r_rads);
  cmdMessenger.sendCmdEnd();
}
void on_request_control_signal(){
  cmdMessenger.sendCmdStart(send_control_sig);
  cmdMessenger.sendCmdBinArg(m1l_pwm); cmdMessenger.sendCmdBinArg(m2l_pwm); cmdMessenger.sendCmdBinArg(m3l_pwm);
  cmdMessenger.sendCmdBinArg(m1r_pwm); cmdMessenger.sendCmdBinArg(m2r_pwm); cmdMessenger.sendCmdBinArg(m3r_pwm);
  cmdMessenger.sendCmdEnd();
}
void attachCommandCallbacks() { // Callbacks define on which received commands we take action
  cmdMessenger.attach(cmd_off, turn_off);
  cmdMessenger.attach(receive_ref, take_ref);
  cmdMessenger.attach(change_kp, on_change_kp);
  cmdMessenger.attach(change_ki, on_change_ki);
  cmdMessenger.attach(request_ticks, on_request_ticks);
  cmdMessenger.attach(request_control_signal, on_request_control_signal);
}


void setup() {
  Serial.begin(115200); // 115200 is the max speed on Arduino Uno
  cmdMessenger.printLfCr();  // Adds newline to every command
  attachCommandCallbacks();  // Attach my application's user-defined callback methods

  // reset Timer 1
  TCCR1A = 0;
  TCCR1B = 0;
  // zero it
  TCNT1 = 0;
  // start Timer 1
  OCR1A  = 255; //Count 255 cycles (prescaled with...)
  TCCR1B =  bit (WGM12) | bit (CS12) | bit (CS10);  //  1024 prescale

  // reset Timer 2
  TCCR2A = 0;
  TCCR2B = 0;
  // zero it
  TCNT2 = 0;
  overflowCount = 0;
  // start Timer 2
  TCCR2B =  bit (CS10);  //  no prescaling

  //Debug leds
  pinMode(led1,OUTPUT);
  digitalWrite(led1,LOW);
  pinMode(led2,OUTPUT);
  digitalWrite(led2,LOW);

  // Encoders pins init
  pinMode(m1l_encoder, INPUT); pinMode(m2l_encoder, INPUT); pinMode(m3l_encoder, INPUT);
  pinMode(m1r_encoder, INPUT); pinMode(m2r_encoder, INPUT); pinMode(m3r_encoder, INPUT);

  /* Motors pin init */
  pinMode(mL_a, OUTPUT);   pinMode(mL_b, OUTPUT);
  pinMode(m1L_en, OUTPUT); pinMode(m1R_en, OUTPUT);
  pinMode(m2L_en, OUTPUT); pinMode(m2R_en, OUTPUT);
  pinMode(m3L_en, OUTPUT); pinMode(m3R_en, OUTPUT);

  // Timer 2 - interrupt on overflow
  TIMSK2 = bit (TOIE2);   // enable Timer2 Interrupt
  // Timer 1 - interrupt on compare
  TIMSK1 = bit (OCIE1A);   // enable Timer1 Interrupt
  setup_isr();
}

void loop() {
  if (controlling) {
    if (m1l_triggered) {
      unsigned long elapsedTime = m1l_finishTime - m1l_startTime;
      digitalWrite(led1,HIGH);
      digitalWrite(led2,LOW);//debug
      m1l_rads = ((float)0.28/((float)elapsedTime*0.0000000625));  // each tick is 62.5 ns at 16 MHz
      setup_m1l_isr();
    } //else m1l_rads = 0.0;
    if (m1r_triggered) {
      digitalWrite(led1,LOW);
      digitalWrite(led2,HIGH);//debug
      unsigned long elapsedTime = m1r_finishTime - m1r_startTime;
      m1r_rads = ((float)0.28/((float)elapsedTime*0.0000000625));  // each tick is 62.5 ns at 16 MHz
      setup_m1r_isr();
    } //else m1r_rads = 0.0;
    if (m2l_triggered) {
      unsigned long elapsedTime = m2l_finishTime - m2l_startTime;
      m2l_rads = ((float)4480000.0/(float)elapsedTime);  // each tick is 62.5 ns at 16 MHz
      setup_m2l_isr();
    } //else m2l_rads = 0.0;
    if (m2r_triggered) {
      unsigned long elapsedTime = m2r_finishTime - m2r_startTime;
      m2r_rads = ((float)4480000.0/(float)elapsedTime);  // each tick is 62.5 ns at 16 MHz
      setup_m2l_isr();
    } //else m2r_rads = 0.0;
    if (m3l_triggered) {
      digitalWrite(led1,LOW);
      digitalWrite(led2,LOW);//debug
      unsigned long elapsedTime = m3l_finishTime - m3l_startTime;
      m3l_rads = ((float)4480000.0/(float)elapsedTime);  // each tick is 62.5 ns at 16 MHz
      setup_m3l_isr();
    } //else m3l_rads = 0.0;
    if (m3r_triggered) {
      digitalWrite(led1,HIGH);
      digitalWrite(led2,HIGH);//debug
      unsigned long elapsedTime = m3r_finishTime - m3r_startTime;
      m3r_rads = ((float)0.28/((float)elapsedTime*0.0000000625));  // each tick is 62.5 ns at 16 MHz
      setup_m3r_isr();
    } //else m3r_rads = 0.0;

    if (flag_cntl){ //Compute control
      m1l_pwm=control_law(1,left_ref,m1l_rads,i_m1l,sat_err_m1l,t_cntl);
      m1r_pwm=control_law(2,right_ref,m1r_rads,i_m1r,sat_err_m1r,t_cntl);
      m2l_pwm=control_law(3,left_ref,m2l_rads,i_m2l,sat_err_m2l,t_cntl);
      m2r_pwm=control_law(4,right_ref,m2r_rads,i_m2r,sat_err_m2r,t_cntl);
      m3l_pwm=control_law(5,left_ref,m3l_rads,i_m3l,sat_err_m3l,t_cntl);
      m3r_pwm=0;//m3r_pwm=control_law(6,right_ref,m3r_rads,i_m3r,sat_err_m3r,t_cntl);
    //Act
      write_pwm(m1L_en,m1l_pwm, mL_a,mL_b);
      write_pwm(m2L_en,m2l_pwm, mL_a,mL_b);
      write_pwm(m3L_en,m3l_pwm, mL_a,mL_b);
      write_pwm(m1R_en,m1r_pwm, mR_a,mR_b);
      write_pwm(m2R_en,m2r_pwm, mR_a,mR_b);
      //write_pwm(m3R_en,m3r_pwm, mR_a,mR_b);
    //Serial stuff
      detachInterrupt(digitalPinToInterrupt(m1l_encoder));
      detachInterrupt(digitalPinToInterrupt(m2l_encoder));
      detachInterrupt(digitalPinToInterrupt(m3l_encoder));
      detachInterrupt(digitalPinToInterrupt(m1r_encoder));
      detachInterrupt(digitalPinToInterrupt(m2r_encoder));
      detachInterrupt(digitalPinToInterrupt(m3r_encoder));
      TIMSK2 = 0; //overflow interrumpt off
      on_request_ticks();
      on_request_control_signal();
      cmdMessenger.feedinSerialData();  // Process incoming serial data, and perform
      TIMSK2 = bit (TOIE2);   // enable Timer2 overflow Interrupt
      attachInterrupt(digitalPinToInterrupt(m1l_encoder), m1l_isr, RISING);
      attachInterrupt(digitalPinToInterrupt(m2l_encoder), m2l_isr, RISING);
      attachInterrupt(digitalPinToInterrupt(m3l_encoder), m3l_isr, RISING);
      attachInterrupt(digitalPinToInterrupt(m1r_encoder), m1r_isr, RISING);
      attachInterrupt(digitalPinToInterrupt(m2r_encoder), m2r_isr, RISING);
      attachInterrupt(digitalPinToInterrupt(m3r_encoder), m3r_isr, RISING);
      flag_cntl=false;
      TIMSK1 = bit (OCIE1A);   // enable Timer1 Interrupt
    }
    /*if ((m1l_triggered) && (m2l_triggered) && (m3l_triggered) && (m1r_triggered) && (m2r_triggered) && (m3r_triggered) && flag_serial) {
      digitalWrite(led1,HIGH); //DEBUG
      TIMSK2 = 0; //overflow interrumpt off
      TIMSK1 = 0;
      on_request_ticks();
      on_request_control_signal();
      cmdMessenger.feedinSerialData();  // Process incoming serial data, and perform
      TIMSK2 = bit (TOIE2);   // enable Timer2 overflow Interrupt
      TIMSK1 = bit (OCIE1A);   // enable Timer1 Interrupt
      flag_serial=false;
    }*/
    /*if ((m1l_triggered) && (m2l_triggered) && (m3l_triggered) && (m1r_triggered) && (m2r_triggered) && (m3r_triggered)) {
      setup_isr();
    }*/
  } else shutdown_motors();  // Stop controlling and power off motors: reset needed
}

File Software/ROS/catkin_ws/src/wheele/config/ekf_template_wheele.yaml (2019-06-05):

# The frequency, in Hz, at which the filter will output a position estimate. Note that the filter will not begin
# computation until it receives at least one message from one of the inputs. It will then run continuously at the
# frequency specified here, regardless of whether it receives more measurements. Defaults to 30 if unspecified.
frequency: 30

# The period, in seconds, after which we consider a sensor to have timed out. In this event, we carry out a predict
# cycle on the EKF without correcting it. This parameter can be thought of as the minimum frequency with which the
# filter will generate new output. Defaults to 1 / frequency if not specified.
sensor_timeout: 0.1

# ekf_localization_node and ukf_localization_node both use a 3D omnidirectional motion model. If this parameter is
# set to true, no 3D information will be used in your state estimate. Use this if you are operating in a planar
# environment and want to ignore the effect of small variations in the ground plane that might otherwise be detected
# by, for example, an IMU. Defaults to false if unspecified.
two_d_mode: true

# Use this parameter to provide an offset to the transform generated by ekf_localization_node. This can be used for
# future dating the transform, which is required for interaction with some other packages. Defaults to 0.0 if
# unspecified.
transform_time_offset: 0.0

# Use this parameter to provide specify how long the tf listener should wait for a transform to become available. 
# Defaults to 0.0 if unspecified.
transform_timeout: 0.0

# If you're having trouble, try setting this to true, and then echo the /diagnostics_agg topic to see if the node is
# unhappy with any settings or data.
print_diagnostics: true

# Debug settings. Not for the faint of heart. Outputs a ludicrous amount of information to the file specified by
# debug_out_file. I hope you like matrices! Please note that setting this to true will have strongly deleterious
# effects on the performance of the node. Defaults to false if unspecified.
debug: false

# Defaults to "robot_localization_debug.txt" if unspecified. Please specify the full path.
debug_out_file: /path/to/debug/file.txt

# Whether to broadcast the transformation over the /tf topic. Defaults to true if unspecified.
publish_tf: true

# Whether to publish the acceleration state. Defaults to false if unspecified.
publish_acceleration: false

# REP-105 (http://www.ros.org/reps/rep-0105.html) specifies four principal coordinate frames: base_link, odom, map, and
# earth. base_link is the coordinate frame that is affixed to the robot. Both odom and map are world-fixed frames.
# The robot's position in the odom frame will drift over time, but is accurate in the short term and should be
# continuous. The odom frame is therefore the best frame for executing local motion plans. The map frame, like the odom
# frame, is a world-fixed coordinate frame, and while it contains the most globally accurate position estimate for your
# robot, it is subject to discrete jumps, e.g., due to the fusion of GPS data or a correction from a map-based
# localization node. The earth frame is used to relate multiple map frames by giving them a common reference frame.
# ekf_localization_node and ukf_localization_node are not concerned with the earth frame.
# Here is how to use the following settings:
# 1. Set the map_frame, odom_frame, and base_link frames to the appropriate frame names for your system.
#     1a. If your system does not have a map_frame, just remove it, and make sure "world_frame" is set to the value of
#         odom_frame.
# 2. If you are fusing continuous position data such as wheel encoder odometry, visual odometry, or IMU data, set
#   "world_frame" to your odom_frame value. This is the default behavior for robot_localization's state estimation nodes.
# 3. If you are fusing global absolute position data that is subject to discrete jumps (e.g., GPS or position updates
# from landmark observations) then:
#     3a. Set your "world_frame" to your map_frame value
#     3b. MAKE SURE something else is generating the odom->base_link transform. Note that this can even be another state
#         estimation node from robot_localization! However, that instance should *not* fuse the global data.
map_frame: map              # Defaults to "map" if unspecified
odom_frame: odom            # Defaults to "odom" if unspecified
base_link_frame: base_link  # Defaults to "base_link" if unspecified
world_frame: odom           # Defaults to the value of odom_frame if unspecified
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

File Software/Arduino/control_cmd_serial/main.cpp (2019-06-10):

#include <Arduino.h>
#include <string.h>
#include <CmdMessenger.h>

/*
ENABLE(PWM) |      A       |     B        |   STATUS           |
---------------------------------------------------------      |
     LOW    |    ----      |    ----      |MOTOR PARADO        |
     HIGH   |    HIGH      |     LOW      |MOTOR GIRA DELANTE  |
     HIGH   |    LOW       |     HIGH     |MOTOR GIRA AL REVES |
     HIGH   |    HIGH      |     HIGH     |MOTOR PARADO        |
     HIGH   |    LOW       |     LOW      |MOTOR PARADO        |
 */

/* Define the pin numbers */
#define mL_a 4
#define mL_b 2

#define m3L_en 6
#define m2L_en 5
#define m1L_en 3

#define mR_a 7
#define mR_b 8

#define m3R_en 9
#define m2R_en 10
#define m1R_en 11

bool controlling = 1; // 1 if control active & motors can run

// Attach a new CmdMessenger object to the default Serial port
CmdMessenger cmdMessenger = CmdMessenger(Serial);

enum {
  cmd_off,  // Cmd to deactivate control & motors. Reset needed after this
  change_pwm,      // Cmd to change velocities, with left motors vel and right motors vel as arguments (float32)
};

/* function to write pwm 2 motors & manage directions */
void write_pwm(int enable,int pwm, int dir1, int dir2){
    if(pwm > 0){
      if (pwm>255) pwm=255;
        digitalWrite(dir1, HIGH);
        digitalWrite(dir2, LOW);
        analogWrite(enable, pwm);
    }
    else if(pwm < 0){
      if (pwm<-255) pwm=-255;
        digitalWrite(dir1, LOW);
        digitalWrite(dir2, HIGH);
        analogWrite(enable, abs(pwm));
    }
    else{
        digitalWrite(enable, LOW);
    }
}

void apply_pwm() {
  float m1L_pwm = cmdMessenger.readBinArg<float>(); // Front left motor pwm
  write_pwm(m1L_en, m1L_pwm, mL_a,mL_b);

  float m1R_pwm = cmdMessenger.readBinArg<float>();  // Front right motor pwm
  write_pwm(m1R_en, m1R_pwm, mR_a,mR_b);

  float m2L_pwm = cmdMessenger.readBinArg<float>(); // Mid left motor pwm
  write_pwm(m2L_en, m2L_pwm, mL_a,mL_b);

  float m2R_pwm = cmdMessenger.readBinArg<float>();  //  Mid right motor pwm
  write_pwm(m2R_en, m2R_pwm, mR_a,mR_b);

  float m3L_pwm = cmdMessenger.readBinArg<float>(); // Back left motor pwm
  write_pwm(m3L_en, m3L_pwm, mL_a,mL_b);

  float m3R_pwm = cmdMessenger.readBinArg<float>();  // Back right motor pwm
  write_pwm(m3R_en, m3R_pwm, mR_a,mR_b);
}

void turn_off() {
  controlling = ! controlling; // Turn off control and motors
}

void shutdown_motors() { // Apagar los motores
  write_pwm(m1L_en,0, mL_a,mL_b);
  write_pwm(m2L_en,0, mL_a,mL_b);
  write_pwm(m3L_en,0, mL_a,mL_b);

  write_pwm(m1R_en,0, mR_a,mR_b);
  write_pwm(m2R_en,0, mR_a,mR_b);
  write_pwm(m3R_en,0, mR_a,mR_b);
}

// Callbacks define on which received commands we take action
void attachCommandCallbacks() { // Callbacks define on which received commands we take action
  cmdMessenger.attach(cmd_off, turn_off);
  cmdMessenger.attach(change_pwm, apply_pwm);
}


void setup() {
  /* Motors pin init */
  pinMode(mL_a, OUTPUT); pinMode(mL_b, OUTPUT);
  pinMode(m1L_en, OUTPUT); pinMode(m1R_en, OUTPUT);
  pinMode(m2L_en, OUTPUT); pinMode(m2R_en, OUTPUT);
  pinMode(m3L_en, OUTPUT); pinMode(m3R_en, OUTPUT);

  Serial.begin(115200); // 115200 is the max speed on Arduino Uno

  cmdMessenger.printLfCr();  // Adds newline to every command
  attachCommandCallbacks(); // Attach my application's user-defined callback methods
}

void loop() {

  if (controlling) cmdMessenger.feedinSerialData();  // Process incoming serial data, and perform callbacks
  else shutdown_motors();  // Stop controlling and power off motors: reset needed
  //delay(1000);
}

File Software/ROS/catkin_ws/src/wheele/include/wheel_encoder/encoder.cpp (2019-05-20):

#include <iostream>
#include <pigpio.h>

#include <encoder.hpp>
#include <numeric>

void re_decoder::_turnOffVel(){

   vel=0.0;
   gpioSetTimerFuncEx(enc_timer_ID,TIMEOUT_ENCD,NULL,this);

   return;
}
void re_decoder::_pulse(int gpio, int level, uint32_t tick)
{
   double tmpVel;

   gpioSetTimerFuncEx(enc_timer_ID,TIMEOUT_ENCD,NULL,this);

   lev = level;

   if(lastlev>0){

      delta_t=(double)gpioTick()/1000-last_t;

      tmpVel=((double)(SEP_MUESCAS)/(double)delta_t)*1000; //ticks /s
      tmpVel=tmpVel*(2*PI)/360.0;	// rad/s

      if(delta_t==0.0) tmpVel=0.0;

      buffer_vel.pop_back();
      buffer_vel.insert(buffer_vel.begin(),tmpVel);

      }
   lastlev=lev;
   last_t=gpioTick()/1000;

   vel=std::accumulate(buffer_vel.begin(),buffer_vel.end(),0.0)/(double)buffer_vel.size();

   gpioSetTimerFuncEx(enc_timer_ID,TIMEOUT_ENCD,_zeroVel,this);

   return;

}

void re_decoder::_pulseEx(int gpio, int level, uint32_t tick, void *user)
{
   re_decoder *mySelf = (re_decoder *) user;

   mySelf->_pulse(gpio, level, tick);
}
void re_decoder::_zeroVel(void *userdata){

   re_decoder *self = (re_decoder *) userdata;
   self->_turnOffVel();
}

re_decoder::re_decoder(int gpio)
{
   mygpio = gpio;
   buffer_vel.resize(WDW);

   lev=0;lastlev=-1;
   delta_t=0;last_t=0;vel=.0;

   enc_timer_ID=no_encoders;
   no_encoders++;

   gpioSetMode(mygpio, PI_INPUT);

   gpioSetPullUpDown(mygpio, PI_PUD_UP);

   gpioSetTimerFuncEx(enc_timer_ID,TIMEOUT_ENCD,_zeroVel,this);

   gpioSetAlertFuncEx(mygpio, _pulseEx, this);

}

void re_decoder::re_cancel(void)
{
   gpioSetAlertFuncEx(mygpio, 0, this);
}

double re_decoder::getVel(void){return vel;}

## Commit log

2019-02-24 Anadido el fichero con el analisis de los diferentes metodos de slam. Tambien los datasets para slam RGB-D
2019-02-24 pcb driver motor
    [motor_driver.kicad_pcb, motor_driver.sch]
2019-02-25 diy l293d design in kicad
2019-02-25 one f*** layer pcb finished, with just 3 bridges
    [motor_driver.kicad_pcb, motor_driver.sch]
2019-02-28 Added arduino files to control motors
    [motor_driver.kicad_pcb, motor_driver.sch]
2019-02-28 Added RPi node to control motors with freenet launch
2019-03-01 Modified PCB and added link to txt
    [KiCad.kicad_pcb, KiCad.sch, motor_driver.kicad_pcb]
2019-03-01 motor driver pcb mkII
    [KiCad.kicad_pcb, KiCad.sch, motor_driver.kicad_pcb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]
2019-03-01 added text
    [motor_driver.kicad_pcb]
2019-03-01 added robot in freecad base
    [back.fcstd, back_sides.fcstd, bottom.fcstd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]
2019-03-06 Motor driver mk2 pcb
    [md2.kicad_pcb, md2.sch]
2019-03-06 Added backup
    [md2.kicad_pcb]
2019-03-08 added face robot to freecad filesystem and dc motors "datasheet". In slam methods octomap
    [face.fcstd]
2019-03-08 added arduino code working............ i guess
2019-03-08 Added 9-DOF IMU Datasheet to docs dir
2019-03-09 la placa ya no esta al reves
2019-03-09 cambiando nombres
    [motor_driver.kicad_pcb, motor_driver.sch]
2019-03-12 Anadido catkin al repo, de tal modo que sea posible compilar los nodos desde él. Se ha optado inicialmente por realizar una union de todos los nodos desarrollados en mismo catkin. Por otro lado, se h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
2019-03-18 ponerla wapa
    [md2.kicad_pcb]
2019-03-22 Arduino code with working pin-out added
2019-03-28 node for mpu9250 imu
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2019-03-30 velocidad angular medida. Imagen pin out de RPi3B
2019-04-01 dynamic encoder objects creation
2019-04-01 created ros node that publish encoder read in float32. Must be tested
2019-04-01 Revert "Added comments to code. Must to review implementation of differential model of robot and the ticks transformation to vel"
    This reverts commit f0e9ce22611b0827e1cc02784050179941e1d165.
    [wheele_odom.cpp]
2019-04-01 Created odometry node. Must work more or less fine
2019-04-02 meh, kill me la vida papasito
2019-04-02 init control motors node
2019-04-02 el caos se ha acercado a su fin
2019-04-02 el caos, acabó. LO QUITÉ YA
2019-04-02 ANALISIS CONTROL MOTORES NIVELES. ME RAYA LO DEL LOW-MID-HIGH LEVEL CONTROLS
2019-04-04 added class for magnetometer ak
2019-04-09 Changed package name in ROS,"wheel_encoder"->"wheele". Also, added arduino communication
2019-04-13 Added launch to Kinect in RPi to wheele package. Modification of readme with dependencies too
2019-04-14 Anadido el control con el mando. Ademas de ello partes para la simulacion en gazebo. mas movidad que no recuerdo
    [model.sdf, model.xacro]
2019-04-14 Solventado bug en el calculo de la velocidad para la comunicacion serie
2019-04-14 Modifiacion de la lectura para que meustre de tieso que lee todos los encoders, he comentado la creacion dinamica de los objetos y lo he hecho de tieso a manopla
2019-04-15 Muestreo de los ticks para la caracteristica estatica
2019-04-15 Errores en el codigo y caracteristica estatica en ticks.txt
    [wheel_encoder.cpp]
2019-04-15 he intentado hacer el control y he muerto en el intento
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2019-04-18 publsh imu and mangetometer data
2019-04-28 Modificaciones de los launch de conexion multimaster. Se acabo el zeroconf. Tambien los yaml de config de wheele
2019-04-30 deberia tirar el orb_slam2 monocular
2019-04-30 anadido los configs para rviz mono
2019-04-30 ficheros de configuracio nde rviz para octomap
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2019-05-02 lo del topico de lo de los ticks y eso
2019-05-02 cosas de calibrar jejeXD
2019-05-02 stl encoder file
    [optical_encoder_20160806-5704-fd9p8y-0.stl]
2019-05-02 arduino error
2019-05-02 *.launch edtd to rel paths to wheele
2019-05-02 lo de la velosidad 0 y eso
2019-05-03 cosillas de control 1
2019-05-03 cosillas de los pkg
2019-05-05 control que no se si tira
2019-05-06 ya no se ni lo que mergeo
2019-05-06 pid paralelololo a ojojojojo
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2019-05-06 saber interpretar polos y ceros en bucle cerrado a ojo sobre el plano imaginario discreto para tunear pid a mano kp=0.14 ki=0.2 o mas en vd da un poco igual
2019-05-06 6 controles que compilan
2019-05-08 encoder stl adapted
    [enc_mod.stl]
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2019-05-08 zero vel at wheel_encoder
2019-05-08 fixeando en 1 link hd no fake
    [wheel_encoder.cpp]
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2019-05-08 Added fake laser-scan to rtabmap
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2019-05-08 Added dynamic reconfig control parameters
    [controlParams.cfg]
2019-05-08 ahi seguimos. Modificando un poco el codigo del control
    [controlParams.cfg]
2019-05-08 Publishing error to can know what fckin is happening
    [controlParams.cfg]
2019-05-08 se grafican las lecturas de los encoders con rqt_plot
2019-05-08 lo ultimo que toque de la clase re_decoder antes de irme
2019-05-09 filtrado de velocidad. Sin probar
2019-05-09 Tuneados 3 controladores. Cambia el rango de referenca
    [controlParams.cfg]
2019-05-09 Modificados parametros del control
    [controlParams.cfg]
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2019-05-17 added cmdMessages to src/serial_com.py and Arduino/mega/main.cpp
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2019-05-20 serial & encoders fixes
    [encoder.cpp, wheel_encoder.cpp]
2019-05-21 changed com. Time to fix odom
    [wheel_encoder.cpp, wheele_odom.cpp]
2019-05-21 Added rosbag with ticks to test odometry node
2019-05-21 Odometry node working done. Problems with m/s to rad/s solved... I think so
    [wheele_odom.cpp]
2019-05-22 Imu calibrated. Madgwick filter running. There is a bag to see the result. Must be retuned the caliration.
    [imu_calib.yaml]
2019-05-23 creo que ahora si hay signo en las velocidades jejeje
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2019-05-26 Configuration files camera
    [depth_kinect_calib.yaml, rgb_kinect_calib.yaml]
2019-05-26 modificado launch de freenekt para encontrar lo de lacamra
2019-05-26 nodo de odometria arreglado
    [wheele_odom.cpp]
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2019-06-06 chasis + cosas en latex/sofware. correciones generales en el doc
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
